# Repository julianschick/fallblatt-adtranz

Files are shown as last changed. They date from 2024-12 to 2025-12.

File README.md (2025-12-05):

# Adtranz-Fallblattmodule
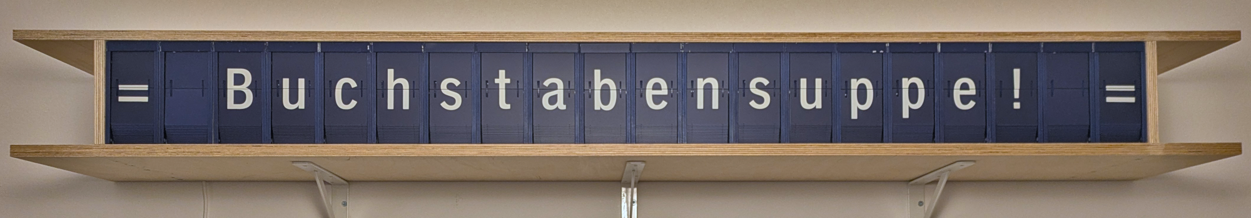
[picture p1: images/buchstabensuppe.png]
Buchstabensuppe


ESP32-Mikrocontrollercode und Leiterplattenlayouts für den Betrieb von 20 Adtranz-Fallblattmodulen mit Alphanumerischer Zeichenpalette.

## Funktionsweise

Wie in [diesem Mikrocontroller.net-Thread](https://www.mikrocontroller.net/topic/460531) auch gut mit Schaltplan erläutert, sind die Fallblattmodule mit einer absoluten Positionierung anhand einer 6-Bit-Gray-Codierungsscheibe versehen. 6 Infrarotdioden sind hinter einer auf der Hauptachse mitrotierenden Scheibe angebracht, deren ringförmige Aussparungen einen Gray-Code ergeben, der mit Infrarotsensoren auf der anderen Seite der Scheibe ausgelesen werden kann.

Meine Ansteuerung besteht aus einem Zentralmodul und einem Steckermodul für jedes einzelne Fallblattmodul. Das Steckermodul bzw. dessen Platine wird mit einen "Card-Edge-Connector" direkt an das Fallblattmodul angesteckt. Auf dem Steckermodul befindet sich lediglich ein Shift-Register und ein Komparatorchip. Der Motor wird, solange mit Betriebsspannung versorgt, solange weiterdrehen, bis der im Shift-Register eingestellte Code auf der Codierungsscheibe erreicht ist.

Auf dem Zentralmodul sitzt ein ESP32, der die als Daisy-Chain verbundenen Steckermodule bzw. deren Shift-Register als ein langes Shift-Register befüllt. Da die Steuerleitungen dieser Shift-Registerkette durchaus lang sind (ca. 2m) ist es erforderlich diese direkt am Ausgang 
des Mikrocontrollers seriell zu terminieren, da die saubere Signalübertragung durch Spiegelungseffekte andernfalls nicht mehr gewährleistet ist.

<div align="center">
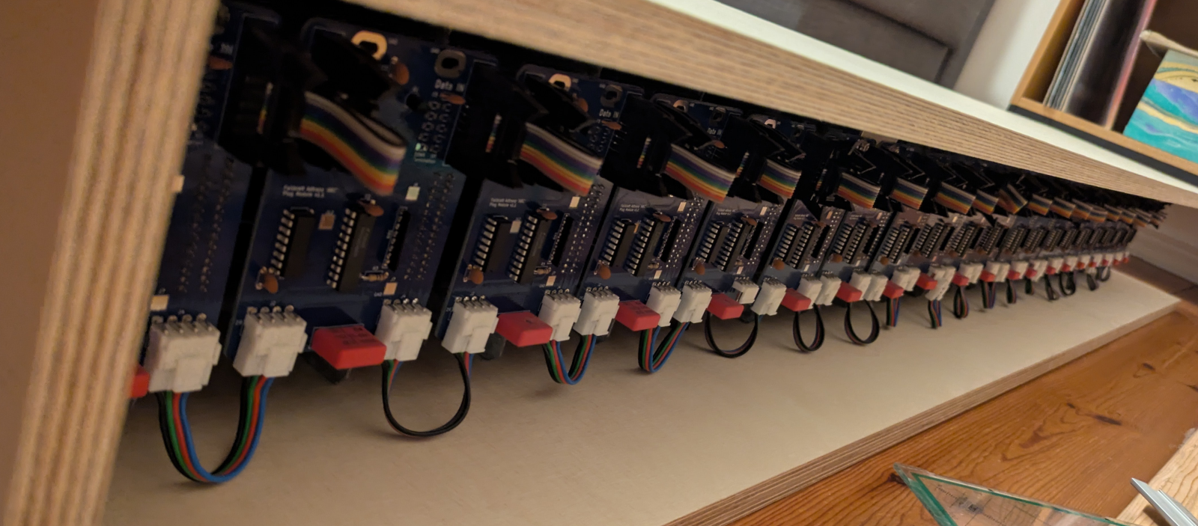
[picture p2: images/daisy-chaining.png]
Daisy-Chaining

</div>

Außerdem war [weitere Stabilisierung nötig](https://www.mikrocontroller.net/topic/573166) bei den Schaltvorgängen des Motor-Relais im Fallblattmoduls. Direkt an den Motor wurde ein 100nF-Entstörkondensator 'angefrankensteint'. Außerdem ist ein 10 Ohm/2,2uF Snubberglied über den Relaiskontakt (zwischen 24 VAC N auf der Steckermodulplatine und 'b' auf der Platine des Fallblattmoduls gelegt) um für Ruhe beim Schalten zu sorgen. Ohne diese Maßnahmen hat die Abschaltung des Motors bei erreichen der gewünschten Stellung der Hauptachse nicht gut funktioniert.

## Leiterplattenlayouts

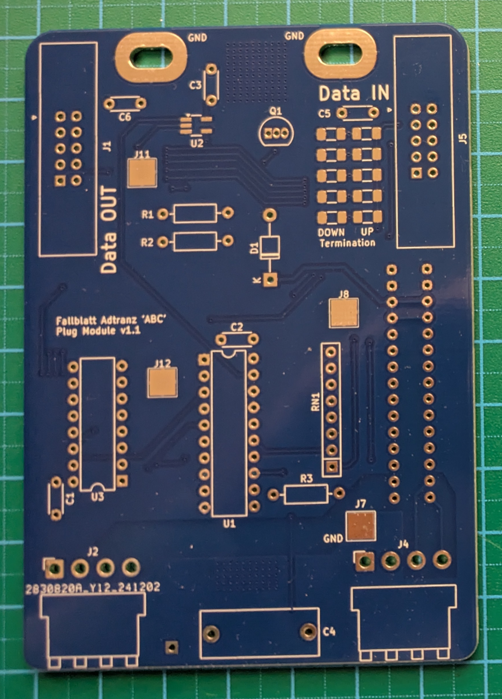
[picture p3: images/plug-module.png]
Steckermodul
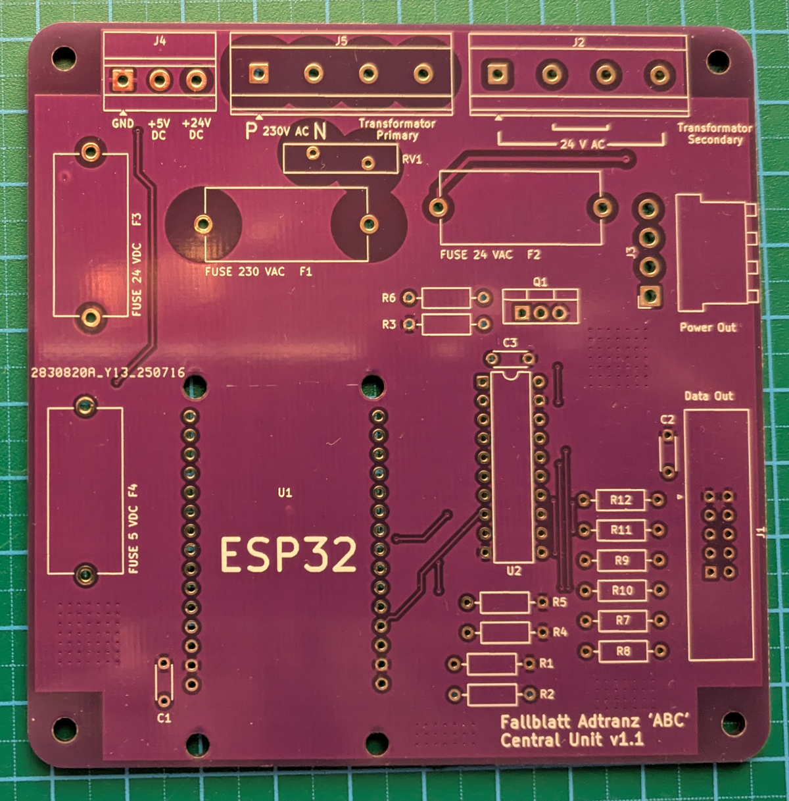
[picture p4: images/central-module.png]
Zentralmodul


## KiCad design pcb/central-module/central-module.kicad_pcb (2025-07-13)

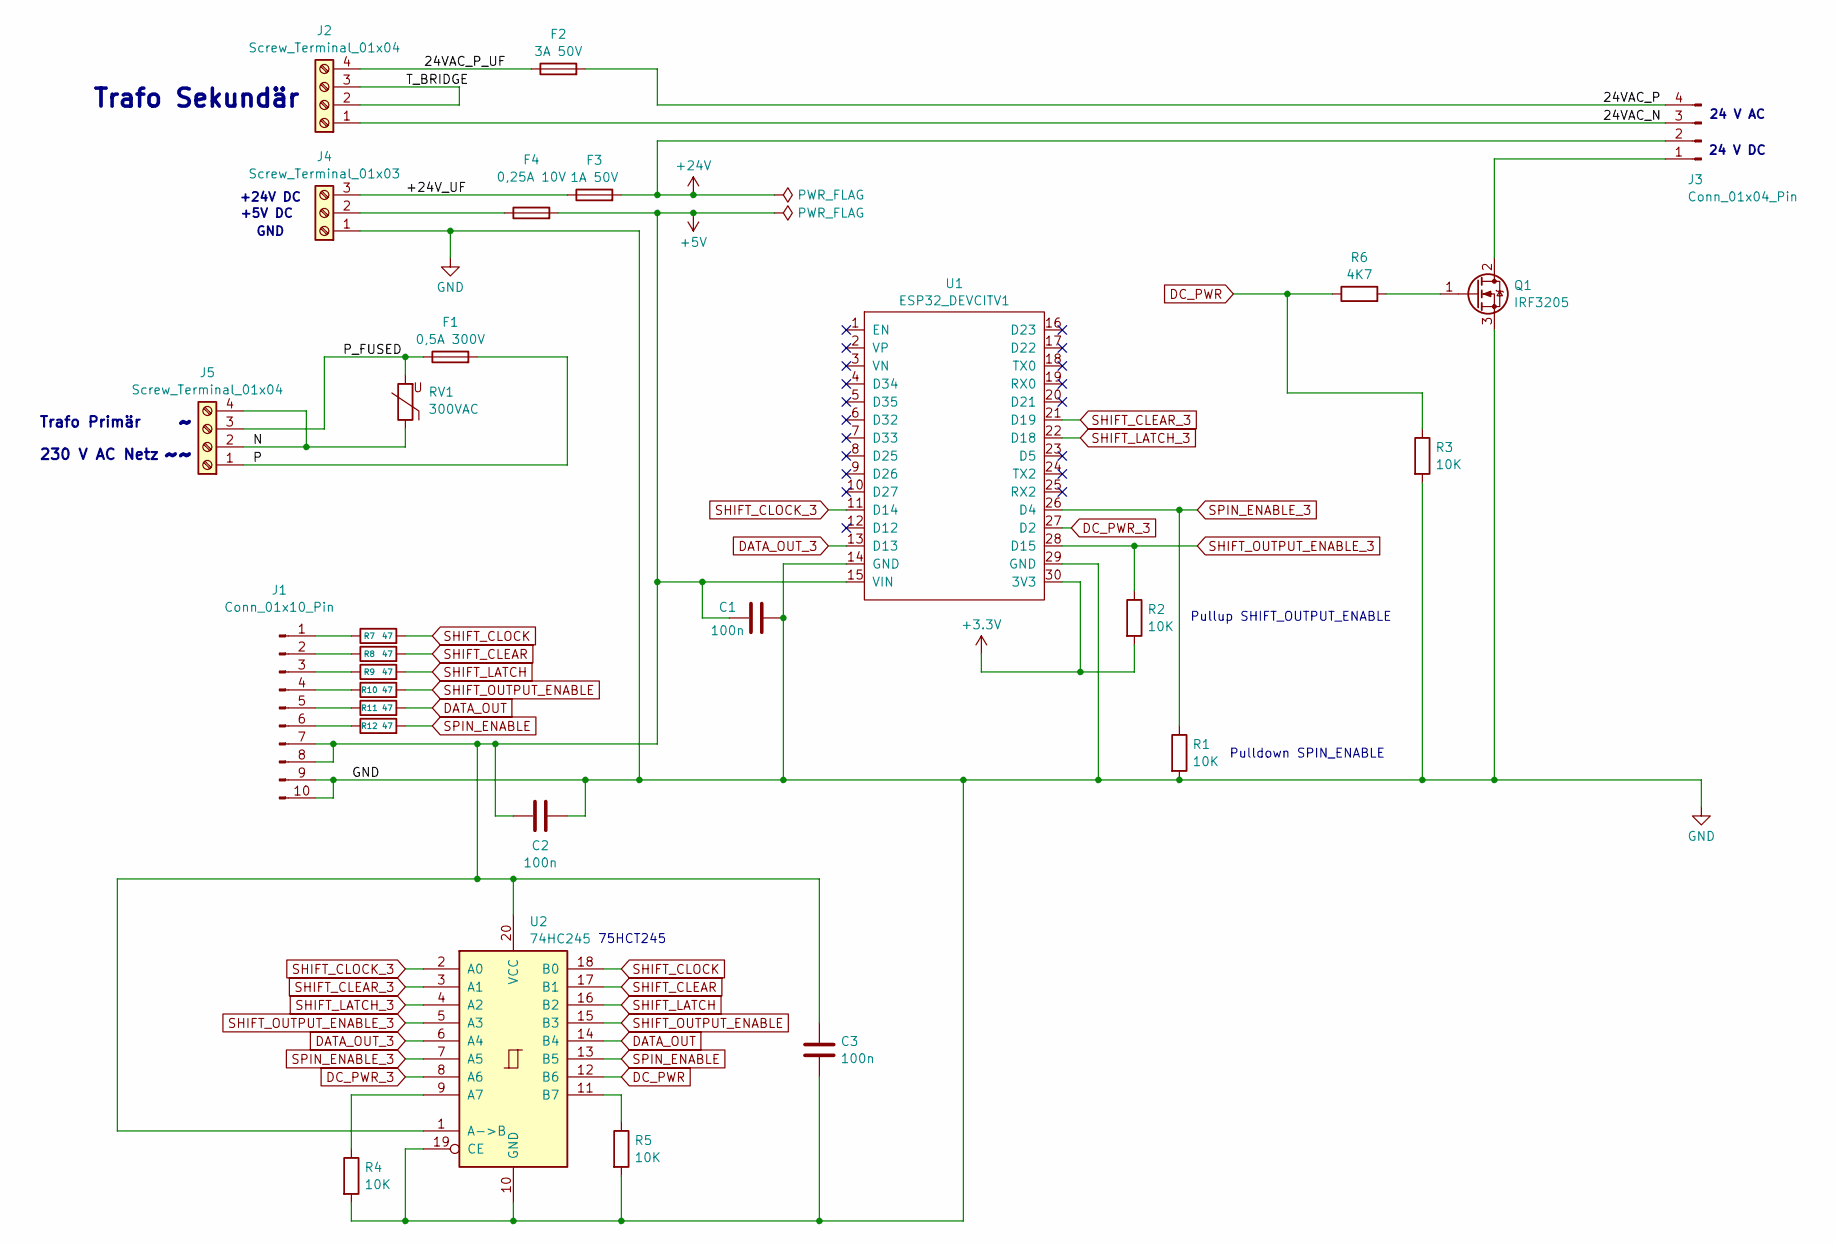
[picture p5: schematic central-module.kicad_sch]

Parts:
C1, C2, C3: 100n; C_Disc_D4.3mm_W1.9mm_P5.00mm
F1: 0,5A 300V; Fuseholder_Schurter_OGN_22.5
F2: 3A 50V; Fuseholder_Schurter_OGN_22.5
F3: 1A 50V; Fuseholder_Schurter_OGN_22.5
F4: 0,25A 10V; Fuseholder_Schurter_OGN_22.5
J1: Conn_01x10_Pin; TE_CON_5499922-1_BIGGERHULL
J2, J5: Screw_Terminal_01x04; TerminalBlock_MetzConnect_Type175_RT02704HBLC_1x04_P7.50mm_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
J3: Conn_01x04_Pin; JST_VH_B4PS-VH_1x04_P3.96mm_Horizontal
J4: Screw_Terminal_01x03; TerminalBlock_MetzConnect_Type011_RT05503HBLC_1x03_P5.00mm_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
Q1: IRF3205; TO-220-3_Vertical
R1, R2, R3, R4, R5: 10K; R_Axial_DIN0207_L6.3mm_D2.5mm_P10.16mm_Horizontal
R6: 4K7; R_Axial_DIN0207_L6.3mm_D2.5mm_P10.16mm_Horizontal
R7, R8, R9, R10, R11, R12: 47; R_Axial_DIN0207_L6.3mm_D2.5mm_P10.16mm_Horizontal
RV1: 300VAC; RV_Disc_D15.5mm_W3.9mm_P7.5mm
U1: ESP32_DEVCITV1; ESP32_DEVKITV1
U2: 74HC245; DIP-20_W7.62mm

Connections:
+3.3V: R2.2, U1.30 (3V3)
+5V: C1.2, C2.2, C3.1, F4.2, J1.7, J1.8, U1.15 (VIN), U2.1 (A->B), U2.20 (VCC)
+24V: F3.2, J3.2
/24VAC_N: J2.1, J3.3
/24VAC_P: F2.2, J3.4
/24VAC_P_UF: F2.1, J2.4
/+24V_UF: F3.1, J4.3
/N: J5.2, J5.4, RV1.1
/P: F1.2, J5.1
/P_FUSED: F1.1, J5.3, RV1.2
/T_BRIDGE: J2.2, J2.3
DATA_OUT: R11.2, U2.14 (B4)
DATA_OUT_3: U1.13 (D13), U2.6 (A4)
DC_PWR: R3.1, R6.1, U2.12 (B6)
DC_PWR_3: U1.27 (D2), U2.8 (A6)
GND: C1.1, C2.1, C3.2, J1.9, J1.10, J4.1, Q1.3 (S), R1.2, R3.2, R4.2, R5.2, U1.14 (GND), U1.29 (GND), U2.10 (GND), U2.19 (CE)
unnamed: J1.1, R7.1
unnamed: J1.2, R8.1
unnamed: J1.3, R9.1
unnamed: J1.4, R10.1
unnamed: J1.5, R11.1
unnamed: J1.6, R12.1
unnamed: J3.1, Q1.2 (D)
unnamed: F4.1, J4.2
unnamed: Q1.1 (G), R6.2
unnamed: R4.1, U2.9 (A7)
unnamed: R5.1, U2.11 (B7)
SHIFT_CLEAR: R8.2, U2.17 (B1)
SHIFT_CLEAR_3: U1.21 (D19), U2.3 (A1)
SHIFT_CLOCK: R7.2, U2.18 (B0)
SHIFT_CLOCK_3: U1.11 (D14), U2.2 (A0)
SHIFT_LATCH: R9.2, U2.16 (B2)
SHIFT_LATCH_3: U1.22 (D18), U2.4 (A2)
SHIFT_OUTPUT_ENABLE: R10.2, U2.15 (B3)
SHIFT_OUTPUT_ENABLE_3: R2.1, U1.28 (D15), U2.5 (A3)
SPIN_ENABLE: R12.2, U2.13 (B5)
SPIN_ENABLE_3: R1.1, U1.26 (D4), U2.7 (A5)

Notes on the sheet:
+24V DC
Pulldown SPIN_ENABLE
24 V AC
24 V DC
75HCT245
230 V AC Netz
+5V DC
Trafo Primär
Pullup SHIFT_OUTPUT_ENABLE
GND
Trafo Sekundär

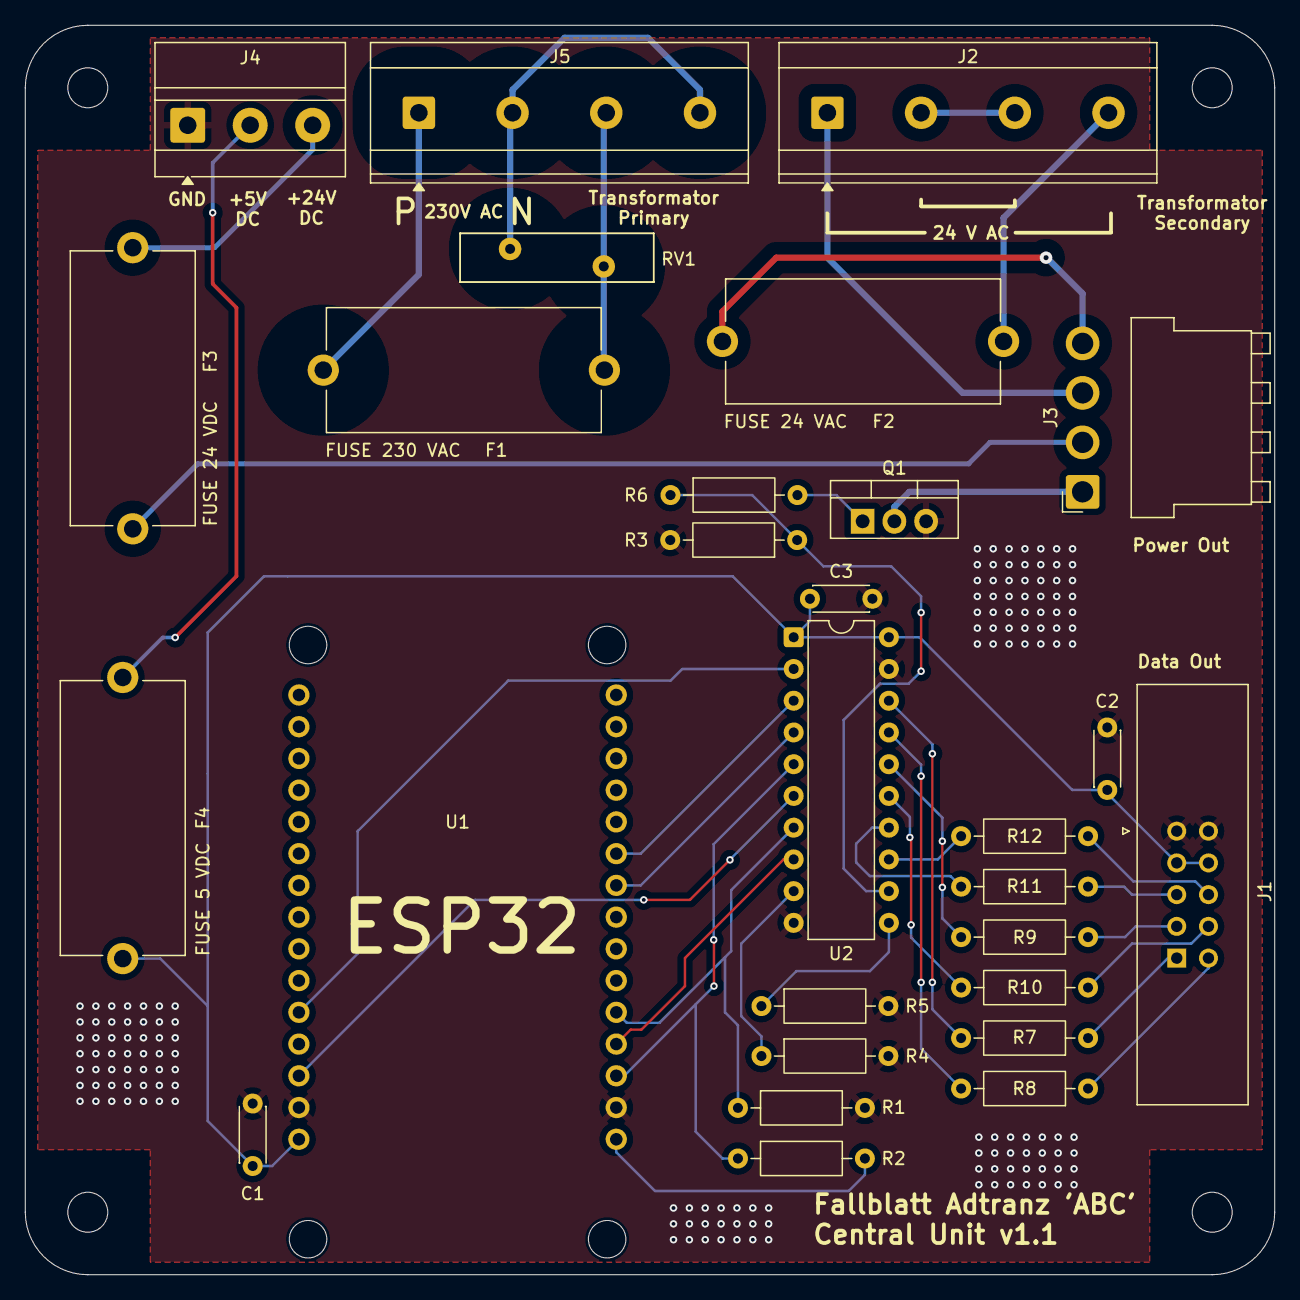
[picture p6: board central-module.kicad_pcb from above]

Board: 2 copper layers, 100.0 x 100.0 mm, 32 parts (0 on the bottom side), 37 nets.

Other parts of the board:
L1, L2, L3, L4: MountingHole_3.2mm_M3

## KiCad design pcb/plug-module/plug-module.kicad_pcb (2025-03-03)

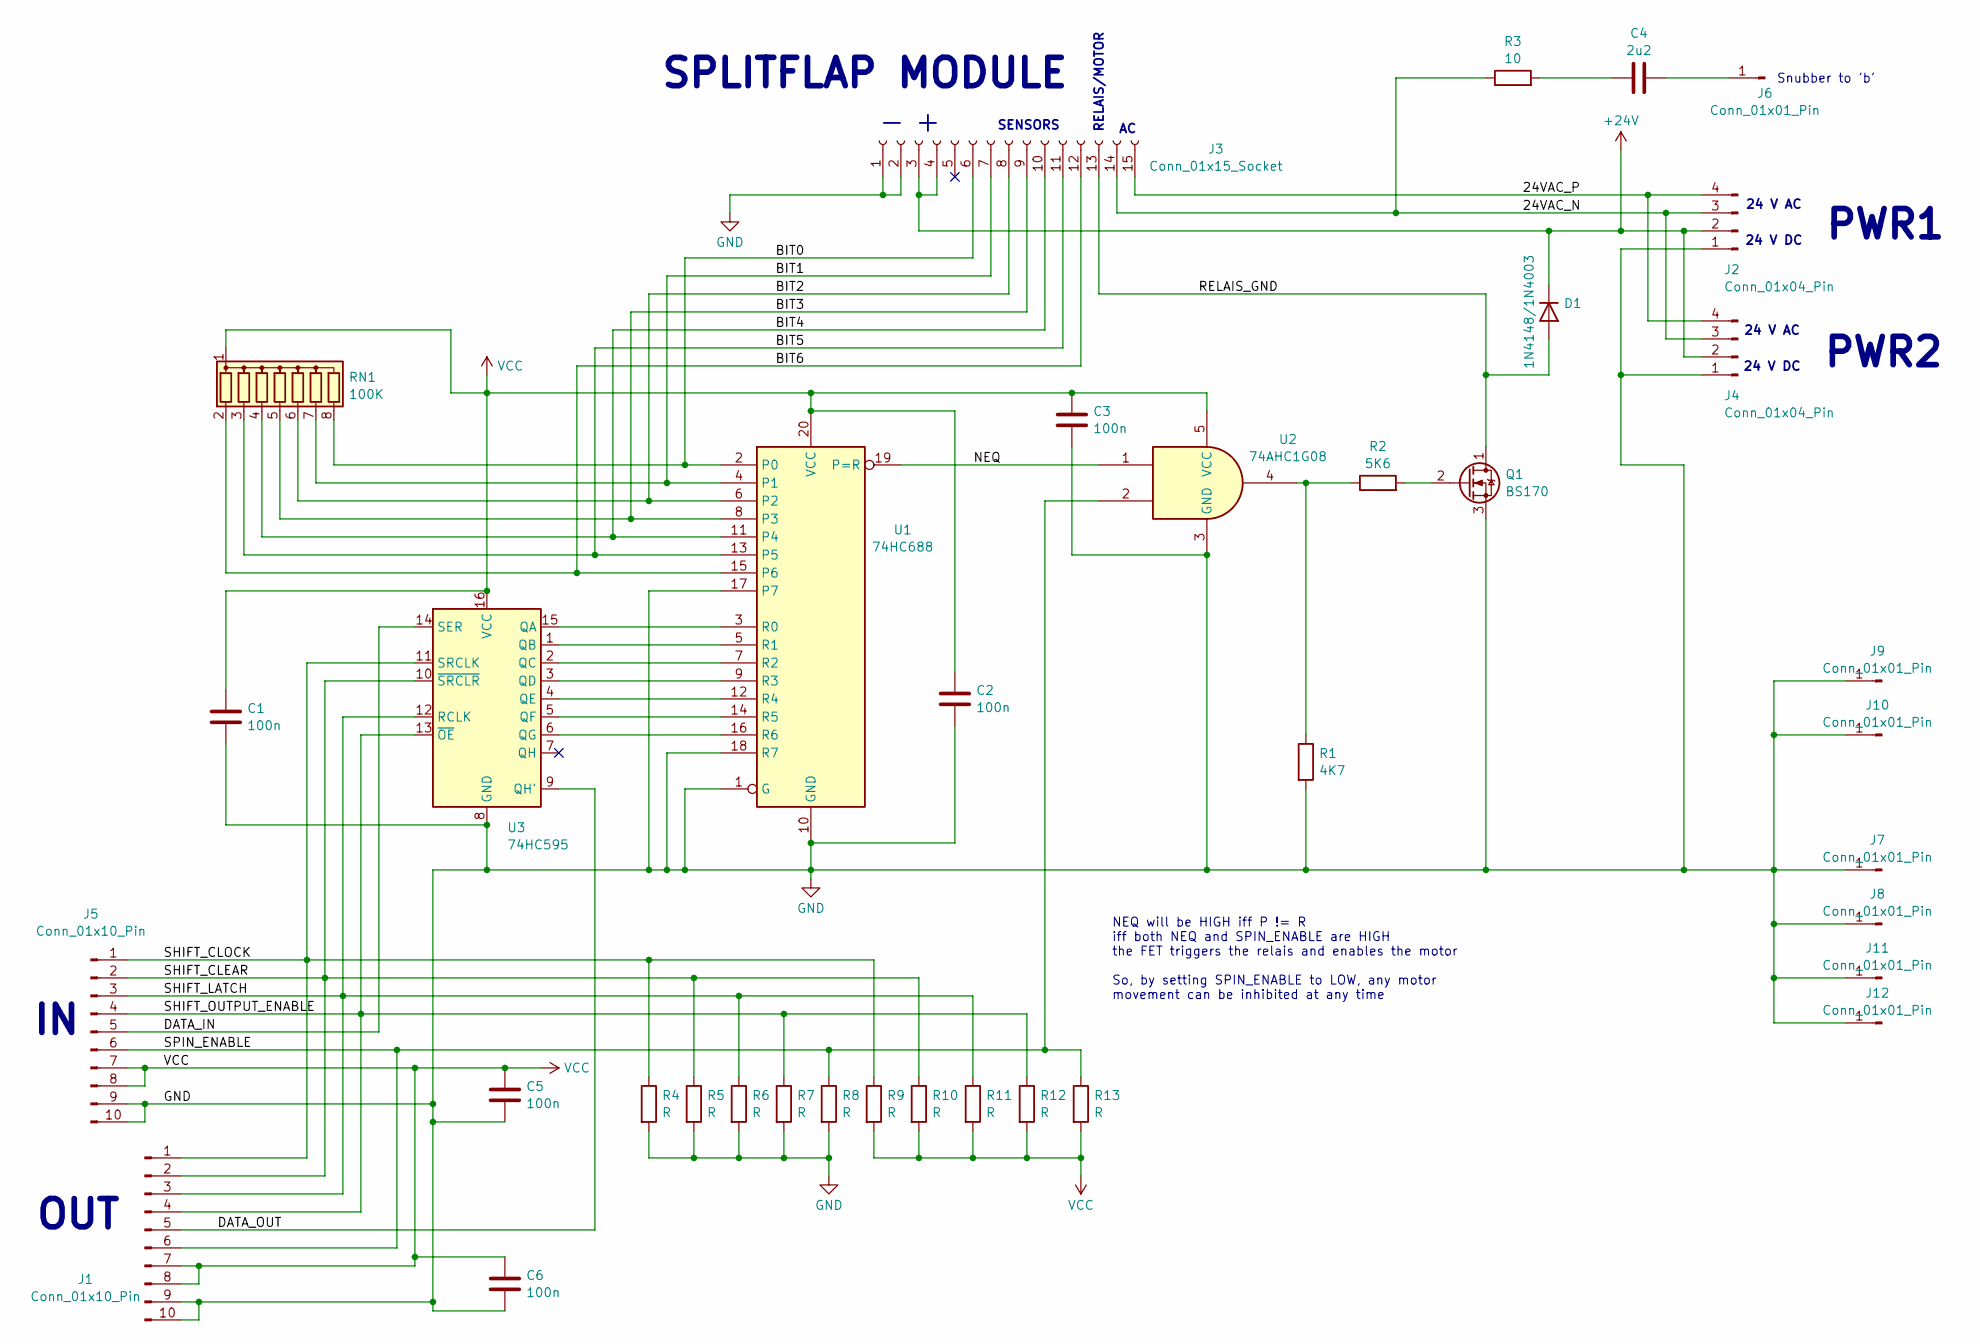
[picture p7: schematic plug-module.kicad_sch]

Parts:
C1, C2, C3, C5, C6: 100n; C_Disc_D4.3mm_W1.9mm_P5.00mm
C4: 2u2; C_Rect_L18.0mm_W7.0mm_P15.00mm_FKS3_FKP3
D1: 1N4148/1N4003; D_T-1_P10.16mm_Horizontal
J1, J5: Conn_01x10_Pin; TE_CON_5499922-1_BIGGERHULL
J2, J4: Conn_01x04_Pin; JST_VH_B4PS-VH_1x04_P3.96mm_Horizontal
J3: Conn_01x15_Socket; 1x15_CardEdge
J6: Conn_01x01_Pin; PinHeader_1x01_P2.54mm_Horizontal
J7, J8, J11, J12: Conn_01x01_Pin; TestPoint_Pad_4.0x4.0mm
J9, J10: Conn_01x01_Pin; Langloch-Pad
Q1: BS170; TO-92_Inline
R1: 4K7; R_Axial_DIN0207_L6.3mm_D2.5mm_P10.16mm_Horizontal
R2: 5K6; R_Axial_DIN0207_L6.3mm_D2.5mm_P10.16mm_Horizontal
R3: 10; R_Axial_DIN0207_L6.3mm_D2.5mm_P10.16mm_Horizontal
R4, R5, R6, R7, R8, R9, R10, R11, R12, R13: R; R_1206_3216Metric_Pad1.30x1.75mm_HandSolder
RN1: 100K; R_Array_SIP8
U1: 74HC688; DIP-20_W7.62mm
U2: 74AHC1G08; TSSOP-5_Handsoldering
U3: 74HC595; DIP-16_W7.62mm

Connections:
+24V: D1.1 (K), J2.2, J3.3, J3.4, J4.2
/24VAC_N: J2.3, J3.14, J4.3, R3.1
/24VAC_P: J2.4, J3.15, J4.4
/BIT0: J3.6, RN1.8 (R7), U1.2 (P0)
/BIT1: J3.7, RN1.7 (R6), U1.4 (P1)
/BIT2: J3.8, RN1.6 (R5), U1.6 (P2)
/BIT3: J3.9, RN1.5 (R4), U1.8 (P3)
/BIT4: J3.10, RN1.4 (R3), U1.11 (P4)
/BIT5: J3.11, RN1.3 (R2), U1.13 (P5)
/BIT6: J3.12, RN1.2 (R1), U1.15 (P6)
/DATA_IN: J5.5, U3.14 (SER)
/DATA_OUT: J1.5, U3.9 (QH')
/NEQ: U1.19 (P=R), U2.1
/RELAIS_GND: D1.2 (A), J3.13, Q1.1 (D)
/SHIFT_CLEAR: J1.2, J5.2, R5.1, R10.1, U3.10 (~SRCLR)
/SHIFT_CLOCK: J1.1, J5.1, R4.1, R9.1, U3.11 (SRCLK)
/SHIFT_LATCH: J1.3, J5.3, R6.1, R11.1, U3.12 (RCLK)
/SHIFT_OUTPUT_ENABLE: J1.4, J5.4, R7.1, R12.1, U3.13 (~OE)
/SPIN_ENABLE: J1.6, J5.6, R8.1, R13.1, U2.2
GND: C1.2, C2.2, C3.2, C5.2, C6.2, J1.9, J1.10, J2.1, J3.1, J3.2, J4.1, J5.9, J5.10, J7.1, J8.1, J9.1, J10.1, J11.1, J12.1, Q1.3 (S), R1.2, R4.2, R5.2, R6.2, R7.2, R8.2, U1.1 (G), U1.10 (GND), U1.17 (P7), U1.18 (R7), U2.3 (GND), U3.8 (GND)
unnamed: C4.1, R3.2
unnamed: C4.2, J6.1
unnamed: Q1.2 (G), R2.2
unnamed: R1.1, R2.1, U2.4
unnamed: U1.3 (R0), U3.15 (QA)
unnamed: U1.5 (R1), U3.1 (QB)
unnamed: U1.7 (R2), U3.2 (QC)
unnamed: U1.9 (R3), U3.3 (QD)
unnamed: U1.12 (R4), U3.4 (QE)
unnamed: U1.14 (R5), U3.5 (QF)
unnamed: U1.16 (R6), U3.6 (QG)
VCC: C1.1, C2.1, C3.1, C5.1, C6.1, J1.7, J1.8, J5.7, J5.8, R9.2, R10.2, R11.2, R12.2, R13.2, RN1.1 (common), U1.20 (VCC), U2.5 (VCC), U3.16 (VCC)

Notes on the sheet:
NEQ will be HIGH iff P != R iff both NEQ and SPIN_ENABLE are HIGH the FET triggers the relais and enables the motor So, by setting SPIN_ENABLE to LOW, any motor movement can be inhibited at any time
PWR2
PWR1
SENSORS
Snubber to 'b'
OUT
24 V DC
24 V AC
RELAIS/MOTOR
SPLITFLAP MODULE

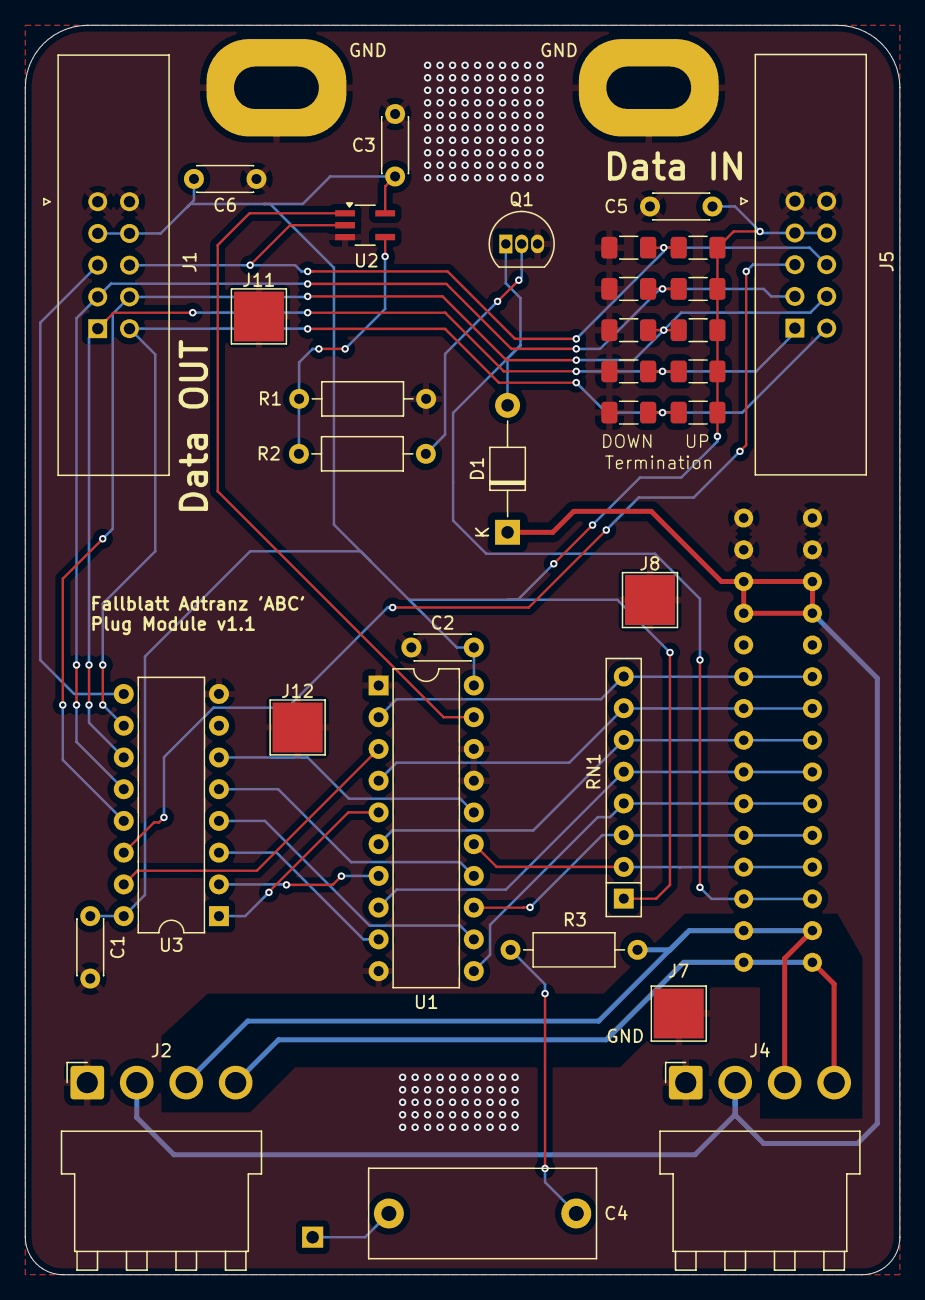
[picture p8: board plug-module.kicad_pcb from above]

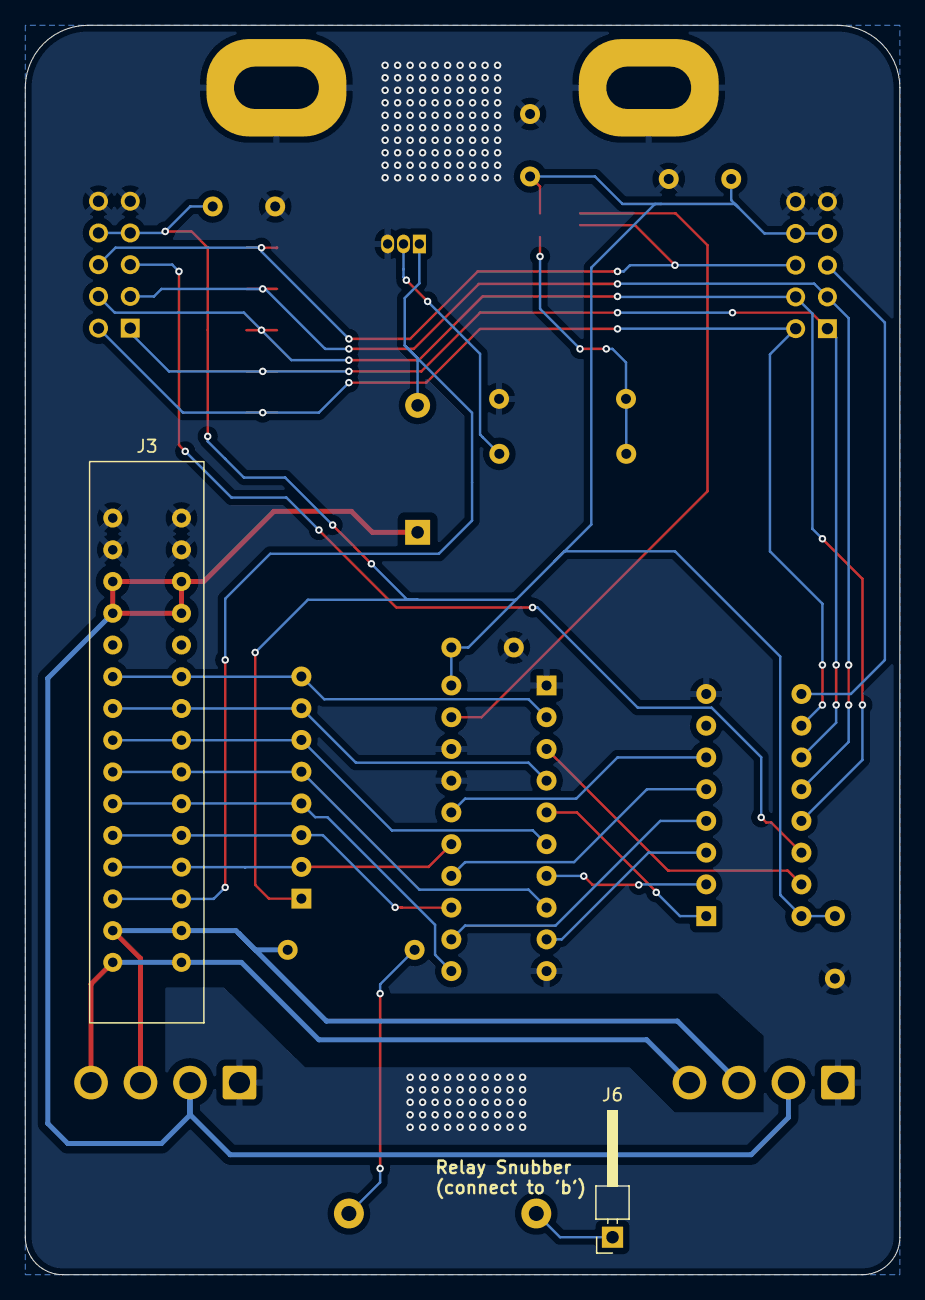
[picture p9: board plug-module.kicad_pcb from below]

Board: 2 copper layers, 70.0 x 100.0 mm, 37 parts (2 on the bottom side), 32 nets.

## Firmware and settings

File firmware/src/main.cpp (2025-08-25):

#include "driver.h"

#include <esp_log.h>
#include <rom/ets_sys.h>
#include <rom/uart.h>

#include <string>
#include <stdexcept>

#include "gray.h"

void main1();
void main2();

extern "C" void app_main() {
    main1();
}

void main2() {
    driver_pins_t pins;
    pins.ser = GPIO_NUM_13;
    pins.serclk = GPIO_NUM_14;
    pins.oe = GPIO_NUM_15;
    pins.clr = GPIO_NUM_19;
    pins.rclk = GPIO_NUM_18;
    pins.spinEnable = GPIO_NUM_4;
    pins.dcEnable = GPIO_NUM_3;

    Driver* drv = new Driver(&pins, 1);

    drv->set_position(0, 0x66);

    while(true) {
        drv->en();
        vTaskDelay(5000 / portTICK_PERIOD_MS);
        drv->dis();
        vTaskDelay(5000 / portTICK_PERIOD_MS);
    }

}

void main1() {
    driver_pins_t pins;
    pins.ser = GPIO_NUM_13;
    pins.serclk = GPIO_NUM_14;
    pins.oe = GPIO_NUM_15;
    pins.clr = GPIO_NUM_19;
    pins.rclk = GPIO_NUM_18;
    pins.spinEnable = GPIO_NUM_4;

    Driver* drv = new Driver(&pins, 1);
    
    while(true) {
        vTaskDelay(100 / portTICK_PERIOD_MS);

        std::string str;
        
        uint8_t ch = 0;
        while (ch != '\n' && ch != '\r') {
            ETS_STATUS state = uart_rx_one_char(&ch);
            if (ch != '\n' && ch != '\r' && state == ETS_OK) {
                str += ch;
            }
            vTaskDelay(10 / portTICK_PERIOD_MS);
        } 

        if (!str.empty()) {
            if (str == "s") {
                ESP_LOGI("main", "stop");
                drv->dis();
            } else if (str == "g") {
                drv->en(); 
                ESP_LOGI("main", "go");
            } else {

                try {
                    int value = std::stoi(str, nullptr, 10);
                    int gray = gray_table[value];

                    ESP_LOGI("main", "set_position()");
                    ESP_LOG_BUFFER_HEX("main", &gray, 1);
                    drv->set_position(0, gray);

                } catch (void* any) {
                    ESP_LOGE("main", "invalid command");
                }
            }
        }
    }
      //  vTaskDelay(1000 / portTICK_PERIOD_MS);
                
        // for (int i = 0; i < 80; i++) {
        //     drv->en();
        //     ets_delay_us(10000);
        //     drv->dis();
        //     vTaskDelay(1000 / portTICK_PERIOD_MS);
        // }

        
        // drv->set_position(0, 5);
        // ESP_LOGI("MAIN", "Pushing out '5'");
        // vTaskDelay(50000 / portTICK_PERIOD_MS);
}

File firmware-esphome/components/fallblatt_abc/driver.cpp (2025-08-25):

#include "driver.h"

#include <rom/ets_sys.h>
#include <esp_log.h>
#include <esp_timer.h>

#define ESP_IDF 5
#define LOG_TAG "ABC_drv"

Driver::Driver(driver_pins_t* pins_, int device_count_) : 
    device_count(device_count_) 
{
    conv = new GrayConverter();
    pins = *pins_;
    positions = new uint8_t[device_count];

    init_gpio();
    init_spi();
}

Driver::~Driver() {
    delete[] positions;
    delete conv;
}

void Driver::set_position(int module_index, uint8_t pos) {
    if (module_index >= 0 && module_index < device_count) {
        positions[module_index] = pos;
    }
}

void Driver::update() {
    last_update = esp_timer_get_time();
    push_out();
    power_on();
    spin_on();
}

void Driver::loop() {
    if (spinning) {
        int64_t now = esp_timer_get_time();
        if (now - last_update > MAX_SPINNING_SECS * 1000000) {
            spin_off();
            power_off();
        }
    }
}

void Driver::init_spi() {
    // uint64_t mask = 0;
    // mask |= (uint64_t) 0x01 << (uint64_t) pins.ser;
    // mask |= (uint64_t) 0x01 << (uint64_t) pins.serclk;

    // gpio_config_t io_conf;
    // io_conf.intr_type = GPIO_INTR_DISABLE;
    // io_conf.mode = GPIO_MODE_OUTPUT;
    // io_conf.pin_bit_mask = mask;
    // io_conf.pull_down_en = GPIO_PULLDOWN_DISABLE;
    // io_conf.pull_up_en = GPIO_PULLUP_DISABLE;
    // ESP_ERROR_CHECK(gpio_config(&io_conf));

    // gpio_set_level(pins.ser, 0);
    // gpio_set_level(pins.serclk, 0);

    esp_err_t ret;

    spi_bus_config_t bus_config;
    bus_config.miso_io_num = -1;
    bus_config.mosi_io_num = pins.ser;
    bus_config.sclk_io_num = pins.serclk;
    bus_config.quadwp_io_num = -1;
    bus_config.quadhd_io_num = -1;
    bus_config.max_transfer_sz = 0;
    bus_config.flags = SPICOMMON_BUSFLAG_MASTER;
    #if ESP_IDF >= 5
    bus_config.isr_cpu_id = ESP_INTR_CPU_AFFINITY_AUTO;
    #endif 
    bus_config.intr_flags = 0;

    spi_device_interface_config_t device_config;
    device_config.command_bits = 0;
    device_config.address_bits = 0;
    device_config.dummy_bits = 0;
    device_config.mode = 0;
    device_config.clock_source = SPI_CLK_SRC_DEFAULT;
    device_config.duty_cycle_pos = 128; // 50%/50%
    device_config.cs_ena_pretrans = 0;
    device_config.cs_ena_posttrans = 0;
    device_config.clock_speed_hz= 10000; // 10 KHz, no need to hurry
    device_config.input_delay_ns = 0;
    device_config.spics_io_num = -1;
    device_config.flags = 0;
    device_config.queue_size = 1;
    device_config.pre_cb = 0;
    device_config.post_cb = 0;

    ret = spi_bus_initialize(HSPI_HOST, &bus_config, SPI_DMA_DISABLED);
    ESP_ERROR_CHECK(ret);
    ret = spi_bus_add_device(HSPI_HOST, &device_config, &spi);
    ESP_ERROR_CHECK(ret);
}

void Driver::init_gpio() {
    uint64_t mask = 0;
    mask |= (uint64_t) 0x01 << (uint64_t) pins.clr;
    mask |= (uint64_t) 0x01 << (uint64_t) pins.rclk;
    mask |= (uint64_t) 0x01 << (uint64_t) pins.oe;
    mask |= (uint64_t) 0x01 << (uint64_t) pins.spin_enable;
    mask |= (uint64_t) 0x01 << (uint64_t) pins.power;

    gpio_config_t io_conf;
    io_conf.intr_type = GPIO_INTR_DISABLE;
    io_conf.mode = GPIO_MODE_OUTPUT;
    io_conf.pin_bit_mask = mask;
    io_conf.pull_down_en = GPIO_PULLDOWN_DISABLE;
    io_conf.pull_up_en = GPIO_PULLUP_DISABLE;
    ESP_ERROR_CHECK(gpio_config(&io_conf));

    // no spinning
    spin_off();
    power_off();
    
    // enable register output
    gpio_set_level(pins.oe, 0);

    // RCLK and SRCLR on HIGH by default
    gpio_set_level(pins.clr, 1);
    gpio_set_level(pins.rclk, 1);

    // initialize all positions to 0
    for (int i = 0; i < device_count; i++) {
        positions[i] = 0;
    }

}

// void Driver::clear_registers() {
//     gpio_set_level(pins.clr, 0);

//     gpio_set_level(pins.rclk, 0);
//     ets_delay_us(1);
//     gpio_set_level(pins.rclk, 1);

//     gpio_set_level(pins.clr, 1);
// }

void Driver::push_out() {

    uint8_t graycodes[device_count];
    for (int i = 0; i < device_count; i++) {
        graycodes[i] = conv->positionToGray(positions[i]);
    }

    spi_transaction_t tx;
    tx.flags = 0;
    tx.cmd = 0;
    tx.addr = 0;
    tx.length = 8 * device_count;
    tx.rxlength = 0;
    tx.rx_buffer = 0;
    tx.tx_buffer = &graycodes;

    gpio_set_level(pins.rclk, 0);
    ets_delay_us(1);
    ESP_ERROR_CHECK(spi_device_transmit(spi, &tx));
    ets_delay_us(1);
    gpio_set_level(pins.rclk, 1);

    //ESP_LOG_BUFFER_HEX(LOG_TAG, &graycodes, device_count);

    // BANG THE BIT
    // int us = 500;

    // for (int i = 0; i < device_count; i++) {
    //     for (int b = 0; b < 8; b++) {
    //         bool bit = (graycodes[i] << b) & 0x80;

    //         gpio_set_level(pins.ser, bit);
    //         ets_delay_us(us);
    //         gpio_set_level(pins.serclk, 1);
    //         ets_delay_us(us);
    //         gpio_set_level(pins.serclk, 0);
    //         ets_delay_us(us);
    //     }
    //     ets_delay_us(us*2);
    // }
    // gpio_set_level(pins.ser, 0);

    // gpio_set_level(pins.rclk, 0);
    // ets_delay_us(500);
    // gpio_set_level(pins.rclk, 1);

}

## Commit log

2024-12-12 r net 100k
    [plug-module.kicad_sch]
2025-01-01 currents / number of mods
2025-01-05 14 modules, central pcb serial termination
    [central-module.kicad_pcb, central-module.kicad_sch]
2025-01-05 disable dma for spi
2025-03-03 convert to kicad 9
    [central-module.kicad_pcb, plug-module.kicad_pcb]
2025-03-05 central-module.kicad_sch -> kicad 9
    [central-module.kicad_sch]
2025-03-15 full 20 module current measurement and fuses
    [central-module.kicad_pcb, central-module.kicad_sch]
2025-06-29 new terminal blocks 7.5 and schurter fuseholders
    [central-module.kicad_pcb, central-module.kicad_sch]
2025-07-13 central module final v1.1
    [central-module.kicad_pcb, central-module.kicad_sch]
2025-12-05 add daisy-chaining image
